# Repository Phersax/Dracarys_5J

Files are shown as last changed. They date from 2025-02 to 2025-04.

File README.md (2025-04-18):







## About the Project
Welcome to the repository dedicated to the development of a 5-degree-of-freedom anthropomorphic robotic arm inspired by the robots Niryo Ned 2 and Kauda! This project aims to create a modular, fully 3D-printable, and open-source manipulator, making it accessible and reproducible for everyone.

The system uses stepper motors to ensure precise movements and features components manufactured through 3D printing. The hardware includes dedicated drivers and a control board to execute smooth trajectories with trapezoidal motion profiles.

In this repository, you’ll find everything you need: 3D models, electronic schematics, control code, and validation tests. Feel free to contribute, improve, and experiment! 

<p align="center">
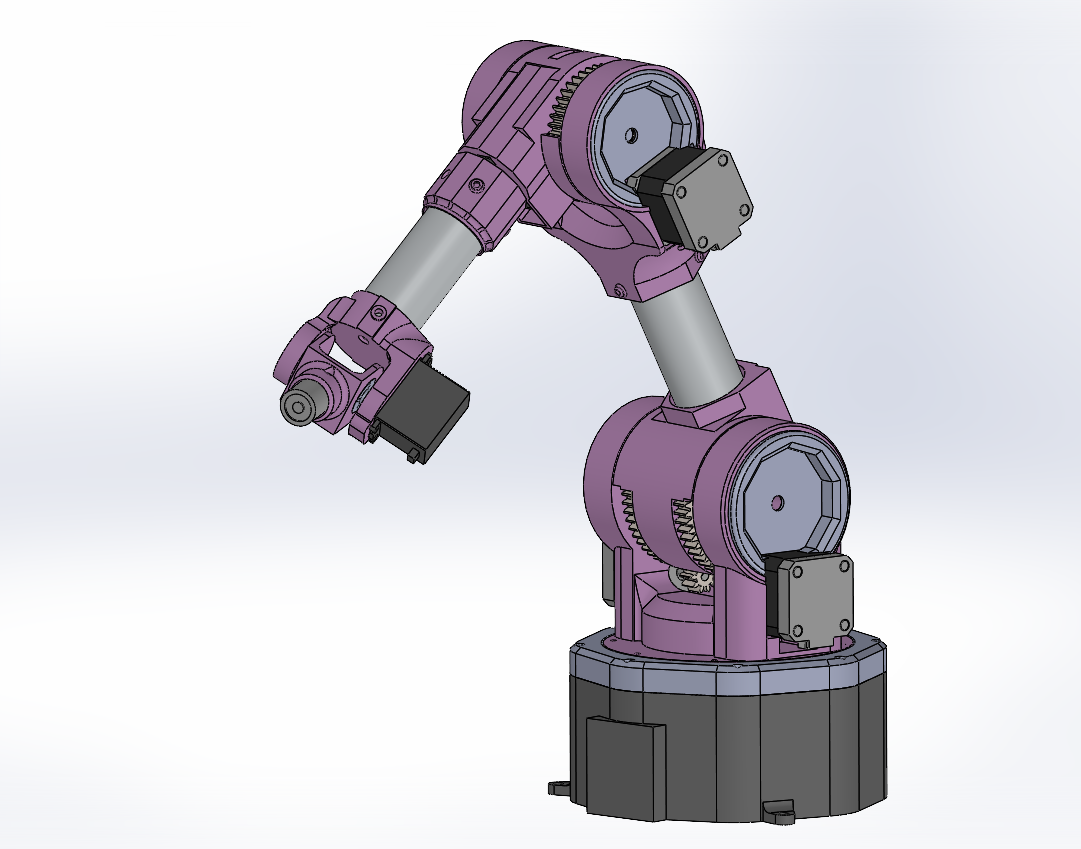
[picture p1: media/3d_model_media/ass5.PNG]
  
</p>

More pictures and videos in the media folder!

## 3D model made with Solidworks
<p align="center">
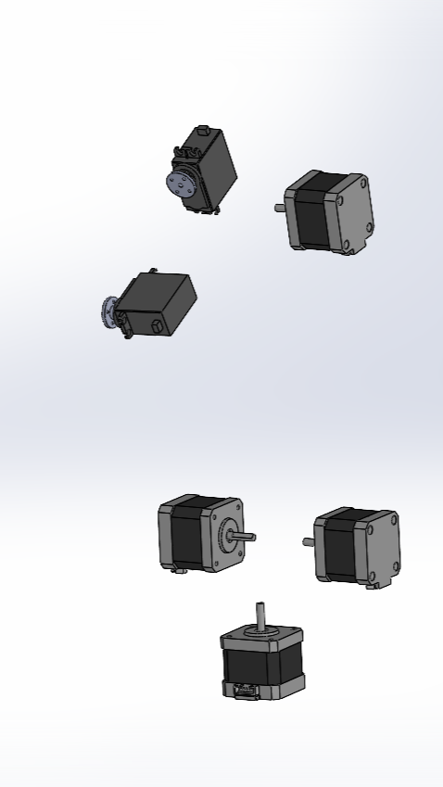
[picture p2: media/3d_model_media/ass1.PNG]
  
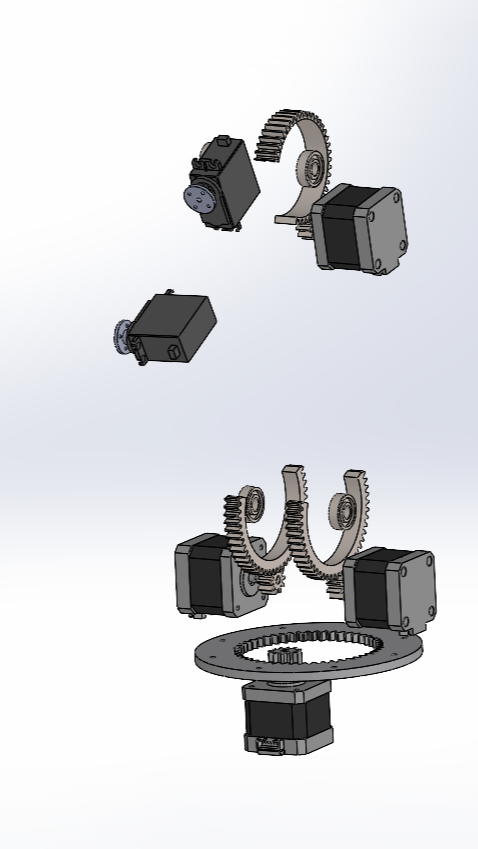
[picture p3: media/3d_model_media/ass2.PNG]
  
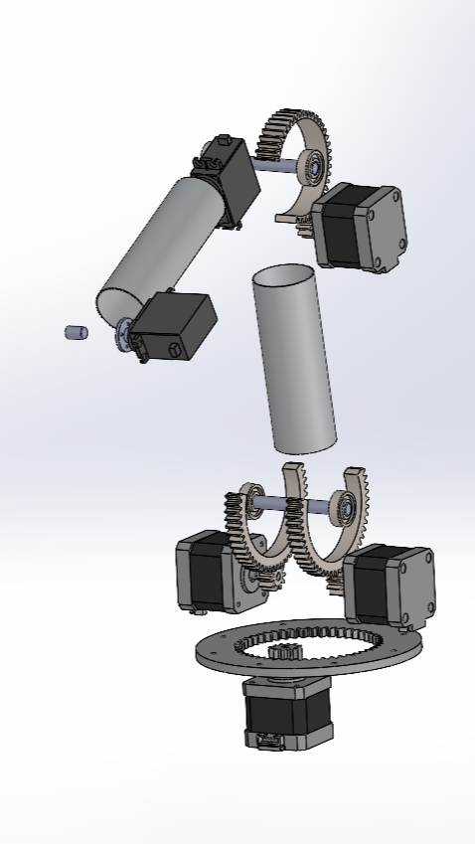
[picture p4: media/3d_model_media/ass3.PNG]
  
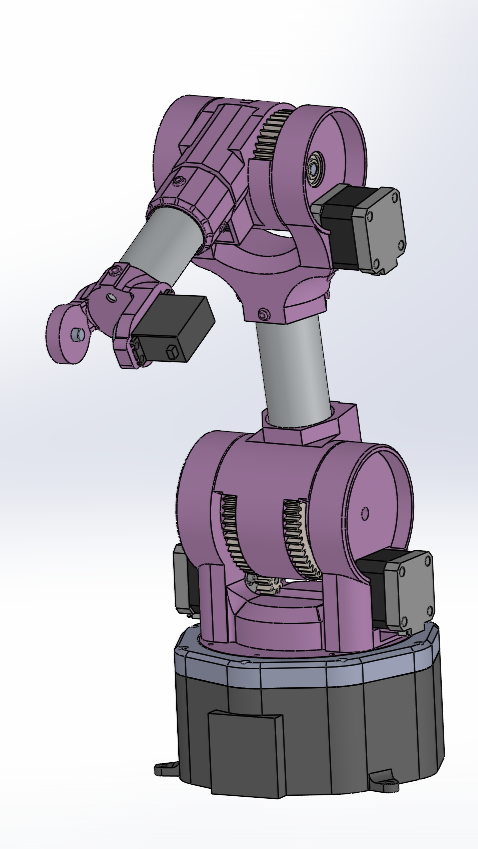
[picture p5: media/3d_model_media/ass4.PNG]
  
</p>

## Schematic
<p align="center">
  
</p>

## Software Notes

All software was developed on the STM32CubeIde and additionally the STM32CubeMx for configuration; for kinematics calculation, on the other hand, MATLAB and the Robotics System Toolbox were used. You may need to download this software in order to load the code properly.

The V1.0_gripper is the main folder of the whole code, anyway you can see for trajectories tested example in the folder v1.0_traj or the 'interrupt_vers' if you're looking for the implementation based on all interrupts. 

If you don't want to use the trapezoidal profile just comment the code as mentioned above, be sure that the timers are set in interrupt mode and check for __HAL_TIM_Base_Start_IT.

For the stepper motor the timers were configured in a chain with master-slave synchronization to count the steps taken according to the rising-edges of the pwm signal and slightly readjusted later to implement the trapezoidal profile. For full configuration details and code insights, links to pdfs are provided in the following section.

The stepper motor control libraries have been implemented to be as general as possible but still refer to the specific manipulator configuration, specifically: 
for joint 1 and joint 3, 1 motor is used; for joint 2, 2 mirrored motors are used, facing each other. Consequently in the stepper library and also partly in the trapezoidal control there are controls for the specific timer of joint 2, which has been treated differently as is the thought configuration. In case one wanted to change software configuration and use for example 1 channel (or 2) for all motors it would be enough to delete (or change) the controls within the libraries and the initial configuration with STM32CubeMx.

## Additional info
Check out the report if you are interested in our work!

[Link to the report](Dr5_report.pdf)

[Link to the pinout and configuration](Dr5_pinout&configuration.pdf)

## License 
Dracarys_5J © 2025 by Francesco Stasi, Davide Tonti is licensed under CC BY-NC-SA 4.0

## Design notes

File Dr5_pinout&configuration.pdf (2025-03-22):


21/03/2025

robotic_arm Project
Configuration Report

## 1. Description

### 1.1. Project

Project Name | robotic_arm
Board Name | NUCLEO-F446RE
Generated with: | STM32CubeMX 6.12.1
Date | 03/21/2025

### 1.2. MCU

MCU Series | STM32F4
MCU Line | STM32F446
MCU name | STM32F446RETx
MCU Package | LQFP64
MCU Pin number | 64

### 1.3. Core(s) information

Core(s) | Arm Cortex-M4

## 2. Pinout Configuration

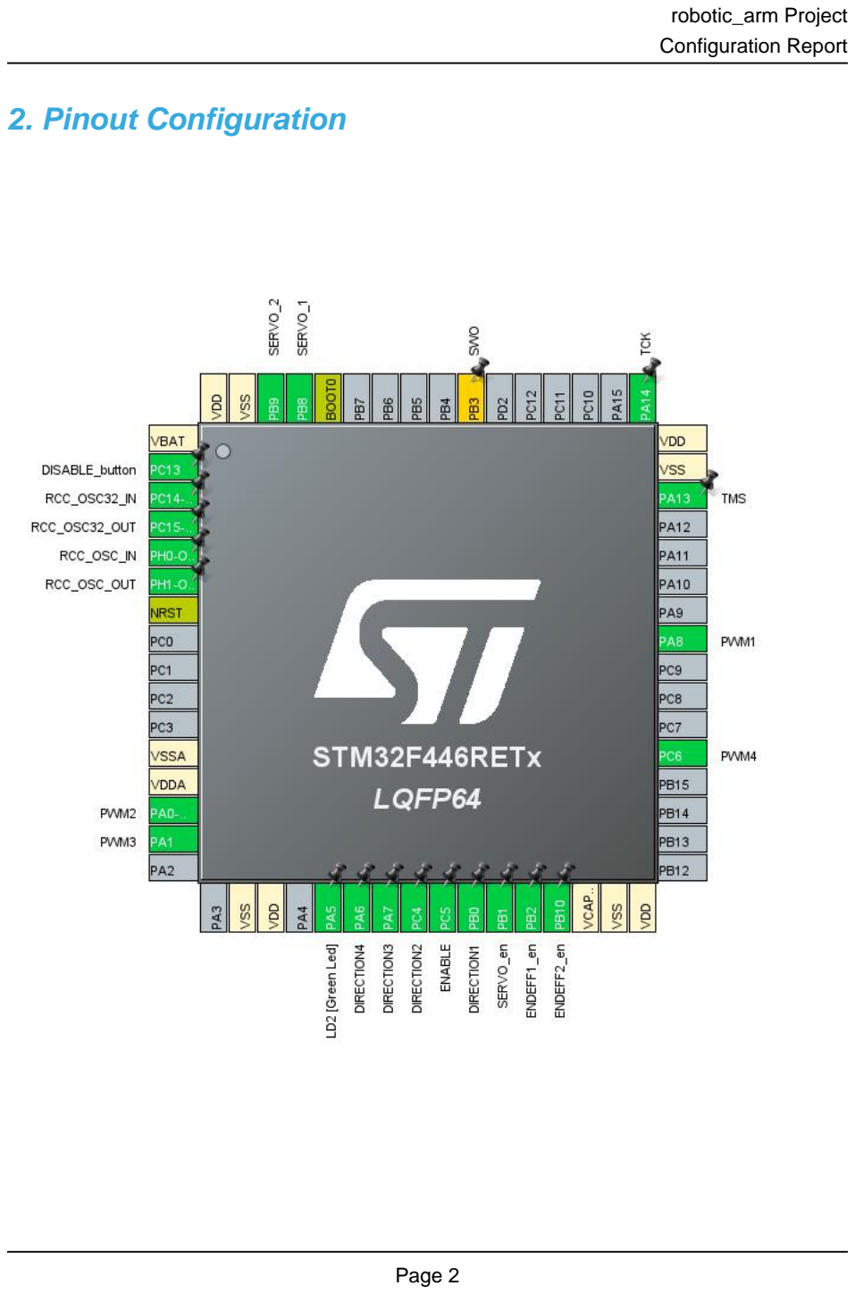
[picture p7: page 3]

## 3. Pins Configuration

Pin Number LQFP64 | Pin Name (function after reset) | Pin Type | Alternate Function(s) | Label
1 | VBAT | Power
2 | PC13 | I/O | GPIO_EXTI13 | DISABLE_button
3 | PC14-OSC32_IN | I/O | RCC_OSC32_IN
4 | PC15-OSC32_OUT | I/O | RCC_OSC32_OUT
5 | PH0-OSC_IN | I/O | RCC_OSC_IN
6 | PH1-OSC_OUT | I/O | RCC_OSC_OUT
7 | NRST | Reset
12 | VSSA | Power
13 | VDDA | Power
14 | PA0-WKUP | I/O | TIM2_CH1 | PWM2
15 | PA1 | I/O | TIM2_CH2 | PWM3
18 | VSS | Power
19 | VDD | Power
21 | PA5 * | I/O | GPIO_Output | LD2 [Green Led]
22 | PA6 * | I/O | GPIO_Output | DIRECTION4
23 | PA7 * | I/O | GPIO_Output | DIRECTION3
24 | PC4 * | I/O | GPIO_Output | DIRECTION2
25 | PC5 * | I/O | GPIO_Output | ENABLE
26 | PB0 * | I/O | GPIO_Output | DIRECTION1
27 | PB1 * | I/O | GPIO_Output | SERVO_en
28 | PB2 * | I/O | GPIO_Output | ENDEFF1_en
29 | PB10 * | I/O | GPIO_Output | ENDEFF2_en
30 | VCAP_1 | Power
31 | VSS | Power
32 | VDD | Power
37 | PC6 | I/O | TIM8_CH1 | PWM4
41 | PA8 | I/O | TIM1_CH1 | PWM1
46 | PA13 | I/O | SYS_JTMS-SWDIO | TMS
47 | VSS | Power
48 | VDD | Power
49 | PA14 | I/O | SYS_JTCK-SWCLK | TCK
55 | PB3 ** | I/O | SYS_JTDO-SWO | SWO
60 | BOOT0 | Boot
61 | PB8 | I/O | TIM10_CH1 | SERVO_1
62 | PB9 | I/O | TIM11_CH1 | SERVO_2
63 | VSS | Power

Pin Number LQFP64 | Pin Name (function after reset) | Pin Type | Alternate Function(s) | Label
64 | VDD | Power

* The pin is affected with an I/O function
** The pin is affected with a peripheral function but no peripheral mode is activated

## 4. Clock Tree Configuration

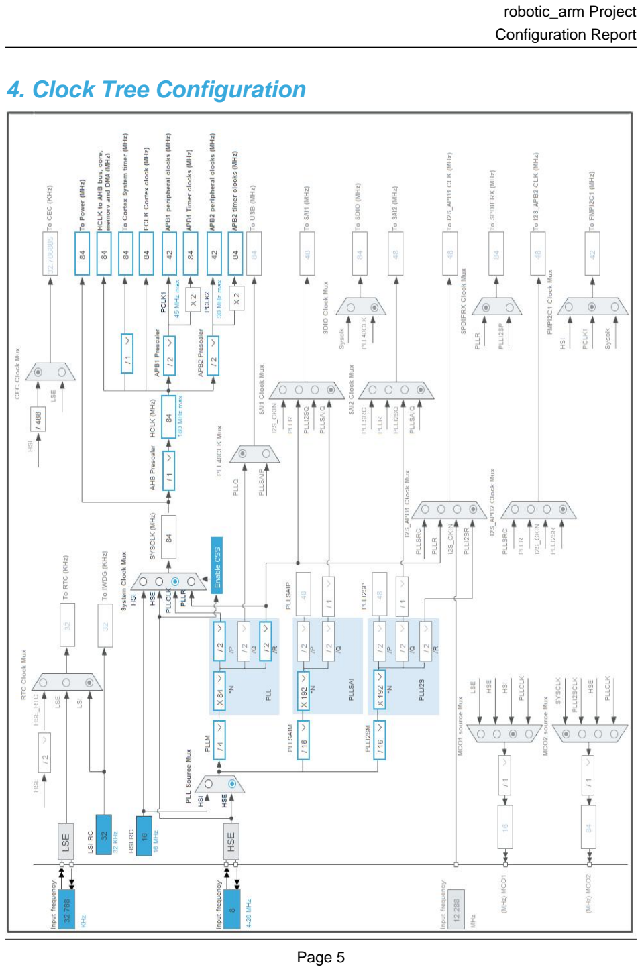
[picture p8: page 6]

## 1. Power Consumption Calculator report

### 1.1. Microcontroller Selection

Series | STM32F4
Line | STM32F446
MCU | STM32F446RETx
Datasheet | DS10693_Rev6

### 1.2. Parameter Selection

Temperature | 25
Vdd | 3.3

### 1.3. Battery Selection

Battery | Li-SOCL2(A3400)
Capacity | 3400.0 mAh
Self Discharge | 0.08 %/month
Nominal Voltage | 3.6 V
Max Cont Current | 100.0 mA
Max Pulse Current | 200.0 mA
Cells in series | 1
Cells in parallel | 1

### 1.4. Sequence

Step | Step1 | Step2
Mode | RUN | STOP_UDM (Under Drive)
Vdd | 3.3 | 3.3
Voltage Source | Battery | Battery
Range | Scale1-High | No Scale
Fetch Type | RAM/FLASH/REGON/ART/P REFETCH | n/a
CPU Frequency | 180 MHz | 0 Hz
Clock Configuration | HSE PLL | Regulator_LP Flash-PwrDwn
Clock Source Frequency | 4 MHz | 0 Hz
Peripherals
Additional Cons. | 0 mA | 0 mA
Average Current | 46 mA | 55 µA
Duration | 0.1 ms | 0.9 ms
DMIPS | 225.0 | 0.0
Ta Max | 98.02 | 104.99
Category | In DS Table | In DS Table

### 1.5. Results

Sequence Time | 1 ms | Average Current | 4.65 mA
Battery Life | 1 month | Average DMIPS | 225.0 DMIPS

### 1.6. Chart

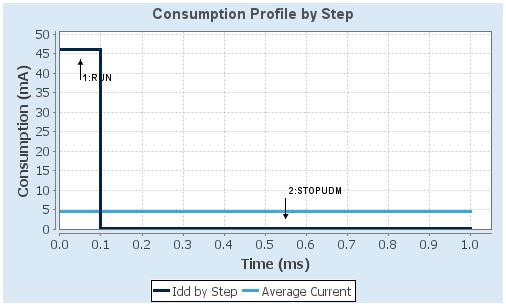
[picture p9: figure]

## 2. Software Project

### 2.1. Project Settings

Name | Value
Project Name | robotic_arm
Project Folder | C:\Users\david\Desktop\v1.0_gripper\Main\robotic_arm
Toolchain / IDE | STM32CubeIDE
Firmware Package Name and Version | STM32Cube FW_F4 V1.28.1
Application Structure | Advanced
Generate Under Root | Yes
Do not generate the main() | No
Minimum Heap Size | 0x200
Minimum Stack Size | 0x400

### 2.2. Code Generation Settings

Name | Value
STM32Cube MCU packages and embedded software | Copy only the necessary library files
Generate peripheral initialization as a pair of '.c/.h' files | Yes
Backup previously generated files when re-generating | No
Keep User Code when re-generating | Yes
Delete previously generated files when not re-generated | Yes
Set all free pins as analog (to optimize the power consumption) | No
Enable Full Assert | No

### 2.3. Advanced Settings - Generated Function Calls

Rank | Function Name | Peripheral Instance Name
1 | SystemClock_Config | RCC
2 | MX_GPIO_Init | GPIO
3 | MX_TIM3_Init | TIM3
4 | MX_TIM5_Init | TIM5
5 | MX_TIM1_Init | TIM1
6 | MX_TIM2_Init | TIM2
7 | MX_TIM4_Init | TIM4
8 | MX_TIM8_Init | TIM8
9 | MX_TIM10_Init | TIM10
10 | MX_TIM11_Init | TIM11
11 | MX_TIM6_Init | TIM6

## 3. Peripherals and Middlewares Configuration

### 3.1. RCC

High Speed Clock (HSE): Crystal/Ceramic Resonator
Low Speed Clock (LSE) : Crystal/Ceramic Resonator
3.1.1. Parameter Settings:

System Parameters:

VDD voltage (V) | 3.3
Instruction Cache | Enabled
Prefetch Buffer | Enabled
Data Cache | Enabled
Flash Latency(WS) | 2 WS (3 CPU cycle)
RCC Parameters:
HSI Calibration Value | 16
TIM Prescaler Selection | Disabled
HSE Startup Timout Value (ms) | 100
LSE Startup Timout Value (ms) | 5000
Power Parameters:
Power Regulator Voltage Scale | Power Regulator Voltage Scale 3
Power Over Drive | Disabled

### 3.2. SYS

Debug: Serial Wire
Timebase Source: SysTick

### 3.3. TIM1

Clock Source : Internal Clock Channel1: PWM Generation CH1
3.3.1. Parameter Settings:

Counter Settings:

Prescaler (PSC - 16 bits value) | 4 *
Counter Mode | Up
Counter Period (AutoReload Register - 16 bits value ) | 65535
Internal Clock Division (CKD) | No Division
Repetition Counter (RCR - 8 bits value) | 0
auto-reload preload | Enable *

Trigger Output (TRGO) Parameters:
Master/Slave Mode (MSM bit) | Enable (Trigger delayed for master/slaves simultaneous start) *
Trigger Event Selection | Update Event *
Break And Dead Time management - BRK Configuration:
BRK State | Disable
BRK Polarity | High
Break And Dead Time management - Output Configuration:
Automatic Output State | Disable
Off State Selection for Run Mode (OSSR) | Disable
Off State Selection for Idle Mode (OSSI) | Disable
Lock Configuration | Off
PWM Generation Channel 1:
Mode | PWM mode 1
Pulse (16 bits value) | 32768 *
Output compare preload | Enable
Fast Mode | Enable *
CH Polarity | High
CH Idle State | Reset

### 3.4. TIM2

Clock Source : Internal Clock Channel1: PWM Generation CH1 Channel2: PWM Generation CH2
3.4.1. Parameter Settings:

Counter Settings:

Prescaler (PSC - 16 bits value) | 4 *
Counter Mode | Up
Counter Period (AutoReload Register - 32 bits value ) | 65535 *
Internal Clock Division (CKD) | No Division
auto-reload preload | Enable *
Trigger Output (TRGO) Parameters:
Master/Slave Mode (MSM bit) | Enable (Trigger delayed for master/slaves simultaneous start) *
Trigger Event Selection | Update Event *
PWM Generation Channel 1:

Mode | PWM mode 1
Pulse (32 bits value) | 32768 *
Output compare preload | Enable
Fast Mode | Enable *
CH Polarity | High
PWM Generation Channel 2:
Mode | PWM mode 1
Pulse (32 bits value) | 32768 *
Output compare preload | Enable
Fast Mode | Enable *
CH Polarity | High

### 3.5. TIM3

Slave Mode: Trigger Mode
Trigger Source: ITR1
Clock Source : Internal Clock
3.5.1. Parameter Settings:

Counter Settings:

Prescaler (PSC - 16 bits value) | 65535 *
Counter Mode | Up
Counter Period (AutoReload Register - 16 bits value ) | 199 *
Internal Clock Division (CKD) | No Division
auto-reload preload | Enable *
Slave Mode Controller | Trigger Mode
Trigger Output (TRGO) Parameters:
Master/Slave Mode (MSM bit) | Disable (Trigger input effect not delayed)
Trigger Event Selection | Reset (UG bit from TIMx_EGR)

### 3.6. TIM4

Slave Mode: Trigger Mode
Trigger Source: ITR0
mode: Clock Source
3.6.1. Parameter Settings:

Counter Settings:

Prescaler (PSC - 16 bits value) | 65535 *
Counter Mode | Up
Counter Period (AutoReload Register - 16 bits value ) | 199 *
Internal Clock Division (CKD) | No Division
auto-reload preload | Enable *
Slave Mode Controller | Trigger Mode
Trigger Output (TRGO) Parameters:
Master/Slave Mode (MSM bit) | Disable (Trigger input effect not delayed)
Trigger Event Selection | Reset (UG bit from TIMx_EGR)

### 3.7. TIM5

Slave Mode: Trigger Mode
Trigger Source: ITR3
mode: Clock Source
3.7.1. Parameter Settings:

Counter Settings:

Prescaler (PSC - 16 bits value) | 65535 *
Counter Mode | Up
Counter Period (AutoReload Register - 32 bits value ) | 199 *
Internal Clock Division (CKD) | No Division
auto-reload preload | Disable
Slave Mode Controller | Trigger Mode
Trigger Output (TRGO) Parameters:
Master/Slave Mode (MSM bit) | Disable (Trigger input effect not delayed)
Trigger Event Selection | Reset (UG bit from TIMx_EGR)

### 3.8. TIM6

mode: Activated
3.8.1. Parameter Settings:

Counter Settings:

Prescaler (PSC - 16 bits value) | 27 *
Counter Mode | Up
Counter Period (AutoReload Register - 16 bits value ) | 1400 *
auto-reload preload | Disable

Trigger Output (TRGO) Parameters:

Trigger Event Selection | Reset (UG bit from TIMx_EGR)

### 3.9. TIM8

Clock Source : Internal Clock
Channel1: PWM Generation CH1
3.9.1. Parameter Settings:

Counter Settings:

Prescaler (PSC - 16 bits value) | 4 *
Counter Mode | Up
Counter Period (AutoReload Register - 16 bits value ) | 65535
Internal Clock Division (CKD) | No Division
Repetition Counter (RCR - 8 bits value) | 0
auto-reload preload | Enable *
Trigger Output (TRGO) Parameters:
Master/Slave Mode (MSM bit) | Enable (Trigger delayed for master/slaves simultaneous start) *
Trigger Event Selection | Update Event *
Break And Dead Time management - BRK Configuration:
BRK State | Disable
BRK Polarity | High
Break And Dead Time management - Output Configuration:
Automatic Output State | Disable
Off State Selection for Run Mode (OSSR) | Disable
Off State Selection for Idle Mode (OSSI) | Disable
Lock Configuration | Off
PWM Generation Channel 1:
Mode | PWM mode 1
Pulse (16 bits value) | 32768 *
Output compare preload | Enable
Fast Mode | Enable *
CH Polarity | High
CH Idle State | Reset

### 3.10. TIM10

mode: Activated
Channel1: PWM Generation CH1
3.10.1. Parameter Settings:

Counter Settings:

Prescaler (PSC - 16 bits value) | 0
Counter Mode | Up
Counter Period (AutoReload Register - 16 bits value ) | 65535
Internal Clock Division (CKD) | No Division
auto-reload preload | Enable *
PWM Generation Channel 1:
Mode | PWM mode 1
Pulse (16 bits value) | 1 *
Output compare preload | Enable
Fast Mode | Enable *
CH Polarity | High

### 3.11. TIM11

mode: Activated
Channel1: PWM Generation CH1
3.11.1. Parameter Settings:

Counter Settings:

Prescaler (PSC - 16 bits value) | 0
Counter Mode | Up
Counter Period (AutoReload Register - 16 bits value ) | 65535
Internal Clock Division (CKD) | No Division
auto-reload preload | Enable *
PWM Generation Channel 1:
Mode | PWM mode 1
Pulse (16 bits value) | 1 *
Output compare preload | Enable
Fast Mode | Enable *
CH Polarity | High

* User modified value

## 4. System Configuration

### 4.1. GPIO configuration

IP | Pin | Signal | GPIO mode | GPIO pull/up pull down | Max Speed | User Label
RCC | PC14-OSC32_IN | RCC_OSC32_IN | n/a | n/a | n/a
| PC15-OSC32_OU T | RCC_OSC32_O UT | n/a | n/a | n/a
| PH0-OSC_IN | RCC_OSC_IN | n/a | n/a | n/a
| PH1-OSC_OUT | RCC_OSC_OUT | n/a | n/a | n/a
SYS | PA13 | SYS_JTMS-SWDIO | n/a | n/a | n/a | TMS
| PA14 | SYS_JTCK-SWCLK | n/a | n/a | n/a | TCK
TIM1 | PA8 | TIM1_CH1 | Alternate Function Push Pull | No pull-up and no pull-down | Low | PWM1
TIM2 | PA0-WKUP | TIM2_CH1 | Alternate Function Push Pull | No pull-up and no pull-down | Low | PWM2
| PA1 | TIM2_CH2 | Alternate Function Push Pull | No pull-up and no pull-down | Low | PWM3
TIM8 | PC6 | TIM8_CH1 | Alternate Function Push Pull | No pull-up and no pull-down | Low | PWM4
TIM10 | PB8 | TIM10_CH1 | Alternate Function Push Pull | No pull-up and no pull-down | Low | SERVO_1
TIM11 | PB9 | TIM11_CH1 | Alternate Function Push Pull | No pull-up and no pull-down | Low | SERVO_2
Single Mapped Signals | PB3 | SYS_JTDO-SWO | n/a | n/a | n/a | SWO
GPIO | PC13 | GPIO_EXTI13 | External Interrupt Mode with Rising edge trigger detection | No pull-up and no pull-down | n/a | DISABLE_button
| PA5 | GPIO_Output | Output Push Pull | No pull-up and no pull-down | Low | LD2 [Green Led]
| PA6 | GPIO_Output | Output Push Pull | Pull-down * | Low | DIRECTION4
| PA7 | GPIO_Output | Output Push Pull | Pull-down * | Low | DIRECTION3
| PC4 | GPIO_Output | Output Push Pull | Pull-down * | Low | DIRECTION2
| PC5 | GPIO_Output | Output Push Pull | Pull-up * | High * | ENABLE
| PB0 | GPIO_Output | Output Push Pull | Pull-down * | Low | DIRECTION1
| PB1 | GPIO_Output | Output Push Pull | Pull-down * | Low | SERVO_en
| PB2 | GPIO_Output | Output Push Pull | Pull-up * | Low | ENDEFF1_en
| PB10 | GPIO_Output | Output Push Pull | Pull-up * | Low | ENDEFF2_en

### 4.2. DMA configuration

nothing configured in DMA service

### 4.3. NVIC configuration

4.3.1. NVIC
Interrupt Table | Enable | Preenmption Priority | SubPriority
Non maskable interrupt | true | 0 | 0
Hard fault interrupt | true | 0 | 0
Memory management fault | true | 0 | 0
Pre-fetch fault, memory access fault | true | 0 | 0
Undefined instruction or illegal state | true | 0 | 0
System service call via SWI instruction | true | 0 | 0
Debug monitor | true | 0 | 0
Pendable request for system service | true | 0 | 0
System tick timer | true | 0 | 0
TIM1 capture compare interrupt | true | 1 | 0
TIM2 global interrupt | true | 1 | 0
EXTI line[15:10] interrupts | true | 0 | 0
TIM8 break interrupt and TIM12 global interrupt | true | 1 | 0
TIM8 update interrupt and TIM13 global interrupt | true | 1 | 0
TIM8 trigger and commutation interrupts and TIM14 global interrupt | true | 1 | 0
TIM8 capture compare interrupt | true | 1 | 0
TIM6 global interrupt and DAC1, DAC2 underrun error interrupts | true | 0 | 0
PVD interrupt through EXTI line 16 | | unused
Flash global interrupt | | unused
RCC global interrupt | | unused
TIM1 break interrupt and TIM9 global interrupt | | unused
TIM1 update interrupt and TIM10 global interrupt | | unused
TIM1 trigger and commutation interrupts and TIM11 global interrupt | | unused
TIM3 global interrupt | | unused
TIM4 global interrupt | | unused
TIM5 global interrupt | | unused
FPU global interrupt | | unused
4.3.2. NVIC Code generation

Enabled interrupt Table Select for init
sequence ordering
| | Generate IRQ
| | handler | Call HAL handler
Non maskable interrupt | false | true | false
Hard fault interrupt | false | true | false

Enabled interrupt Table | Select for init sequence ordering | Generate IRQ handler | Call HAL handler
Memory management fault | false | true | false
Pre-fetch fault, memory access fault | false | true | false
Undefined instruction or illegal state | false | true | false
System service call via SWI instruction | false | true | false
Debug monitor | false | true | false
Pendable request for system service | false | true | false
System tick timer | false | true | true
TIM1 capture compare interrupt | false | true | true
TIM2 global interrupt | false | true | true
EXTI line[15:10] interrupts | false | true | true
TIM8 break interrupt and TIM12 global interrupt | false | true | true
TIM8 update interrupt and TIM13 global interrupt | false | true | true
TIM8 trigger and commutation interrupts and TIM14 global interrupt | false | true | true
TIM8 capture compare interrupt | false | true | true
TIM6 global interrupt and DAC1, DAC2 underrun error interrupts | false | true | true

* User modified value

## 5. System Views

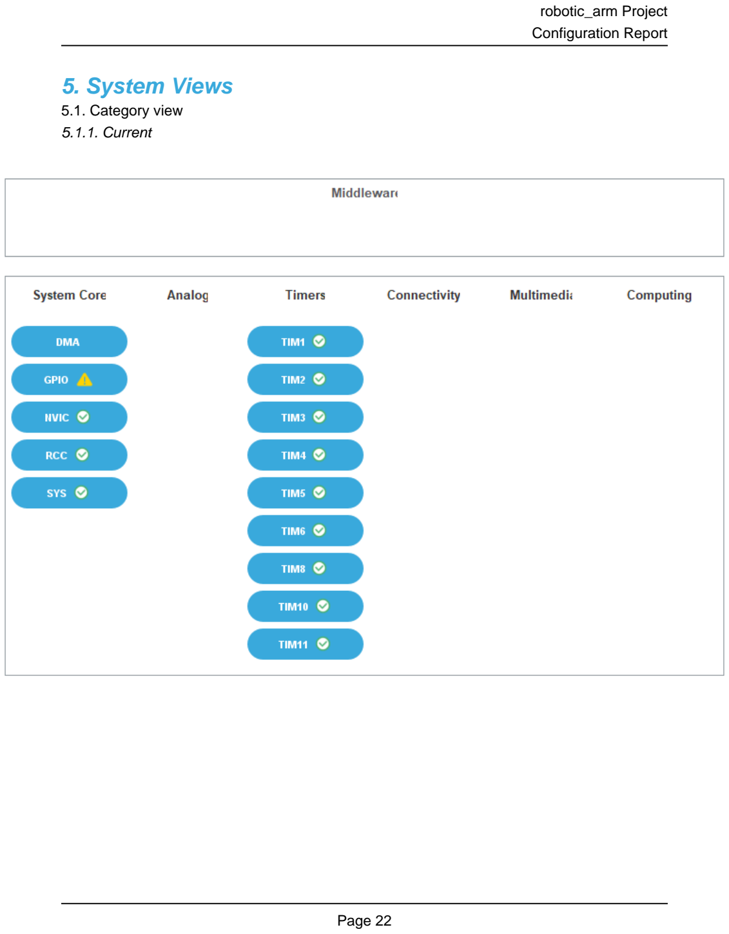
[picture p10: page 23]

5.1. Category view
5.1.1. Current

## 6. Docs & Resources

Type | Link
BSDL files | https://www.st.com/resource/en/bsdl_model/stm32f446_bsdl.zip
IBIS models | https://www.st.com/resource/en/ibis_model/stm32f446_ibis.zip
System View Description | https://www.st.com/resource/en/svd/stm32f4-svd.zip
Presentations | https://www.st.com/resource/en/product_presentation/stm32-stm8_embedded_software_solutions.pdf
Presentations | https://www.st.com/resource/en/product_presentation/stm32_eval-tools_portfolio.pdf
Presentations | https://www.st.com/resource/en/product_presentation/stm32_stm8_functi onal-safety-packages.pdf
Presentations | https://www.st.com/resource/en/product_presentation/stm32-stm8_software_development_tools.pdf
Presentations | https://www.st.com/resource/en/product_presentation/microcontrollers-stm32-family-overview.pdf
Brochures | https://www.st.com/resource/en/brochure/products-and-solutions-for-plcs-and-smart-i-os.pdf
Flyers | https://www.st.com/resource/en/flyer/flstm32nucleo.pdf
Flyers | https://www.st.com/resource/en/flyer/flstm32trust.pdf
Product Certifications | https://www.st.com/resource/en/certification_document/stm32_authentication_can.pdf
Application Notes | https://www.st.com/resource/en/application_note/an1709-emc-design-guide-for-stm8-stm32-and-legacy-mcus-stmicroelectronics.pdf
Application Notes | https://www.st.com/resource/en/application_note/an2606-stm32-microcontroller-system-memory-boot-mode-stmicroelectronics.pdf
Application Notes | https://www.st.com/resource/en/application_note/an2945-stm8s-and-stm32-mcus-a-consistent-832bit-product-line-for-painless-migration-stmicroelectronics.pdf
Application Notes | https://www.st.com/resource/en/application_note/an3070-managing-the- driver-enable-signal-for-rs485-and-iolink-communications-with-the-

| stm32s-usart-stmicroelectronics.pdf
Application Notes | https://www.st.com/resource/en/application_note/an3126-audio-and-waveform-generation-using-the-dac-in-stm32-products-stmicroelectronics.pdf
Application Notes | https://www.st.com/resource/en/application_note/an3154-can-protocol-used-in-the-stm32-bootloader-stmicroelectronics.pdf
Application Notes | https://www.st.com/resource/en/application_note/an3155-usart-protocol-used-in-the-stm32-bootloader-stmicroelectronics.pdf
Application Notes | https://www.st.com/resource/en/application_note/an3156-usb-dfu-protocol-used-in-the-stm32-bootloader-stmicroelectronics.pdf
Application Notes | https://www.st.com/resource/en/application_note/an3364-migration-and-compatibility-guidelines-for-stm32-microcontroller-applications-stmicroelectronics.pdf
Application Notes | https://www.st.com/resource/en/application_note/an3997-audio-playback-and-recording-using-the-stm32f4discovery-stmicroelectronics.pdf
Application Notes | https://www.st.com/resource/en/application_note/an3998-pdm-audio-software-decoding-on-stm32-microcontrollers-stmicroelectronics.pdf
Application Notes | https://www.st.com/resource/en/application_note/an4031-using-the-stm32f2-stm32f4-and-stm32f7-series-dma-controller-stmicroelectronics.pdf
Application Notes | https://www.st.com/resource/en/application_note/an4221-i2c-protocol-used-in-the-stm32-bootloader-stmicroelectronics.pdf
Application Notes | https://www.st.com/resource/en/application_note/an4286-spi-protocol-used-in-the-stm32-bootloader-stmicroelectronics.pdf
Application Notes | https://www.st.com/resource/en/application_note/an4488-getting-started-with-stm32f4xxxx-mcu-hardware-development-stmicroelectronics.pdf
Application Notes | https://www.st.com/resource/en/application_note/an4566-extending-the-dac-performance-of-stm32-microcontrollers-stmicroelectronics.pdf
Application Notes | https://www.st.com/resource/en/application_note/an4640-peripherals-interconnections-on-stm32f4057xx-stm32f4157xx-stm32f42xxx-stm32f43xxx-stm32f446xx-and-stm32f469479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
Application Notes | https://www.st.com/resource/en/application_note/an4655-virtually- increasing-the-number-of-serial-communication-peripherals-in-stm32-

| applications-stmicroelectronics.pdf
Application Notes | https://www.st.com/resource/en/application_note/an4658-migration-of-applications-from-stm32f429439-lines-to-stm32f446-line-stmicroelectronics.pdf
Application Notes | https://www.st.com/resource/en/application_note/an4739-stm32cube-firmware-examples-for-stm32f4-series-stmicroelectronics.pdf
Application Notes | https://www.st.com/resource/en/application_note/an4750-handling-of-soft-errors-in-stm32-applications-stmicroelectronics.pdf
Application Notes | https://www.st.com/resource/en/application_note/an4776-generalpurpose-timer-cookbook-for-stm32-microcontrollers-stmicroelectronics.pdf
Application Notes | https://www.st.com/resource/en/application_note/an4803-highspeed-si-simulations-using-ibis-and-boardlevel-simulations-using-hyperlynx-si-on-stm32-mcus-and-mpus-stmic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
Application Notes | https://www.st.com/resource/en/application_note/an4850-stm32-mcus-spreadspectrum-clock-generation-principles-properties-and-implementation-stmicroelectronics.pdf
Application Notes | https://www.st.com/resource/en/application_note/an4989-stm32-microcontroller-debug-toolbox-stmicroelectronics.pdf
Application Notes | https://www.st.com/resource/en/application_note/an4995-using-an-electromyogram-technique-to-detect-muscle-activity-stmicroelectronics.pdf
Application Notes | https://www.st.com/resource/en/application_note/an5027-interfacing-pdm-digital-microphones-using-stm32-mcus-and-mpus-stmicroelectronics.pdf
Application Notes | https://www.st.com/resource/en/application_note/an5073-receiving-spdif-audio-stream-with-the-stm32f4f7h7-series-stmicroelectronics.pdf
Application Notes | https://www.st.com/resource/en/application_note/an4760-quadspi-interface-on-stm32-microcontrollers-and-microprocessors--stmicroelectronics.pdf
Application Notes | https://www.st.com/resource/en/application_note/an4899-stm32-microcontroller-gpio-hardware-settings-and-lowpower-consumption-stmicroelectronics.pdf
Application Notes | https://www.st.com/resource/en/application_note/an5612-esd-protection-of-stm32-mcus-and-mpus-stmicroelectronics.pdf

Application Notes | https://www.st.com/resource/en/application_note/an4838-introduction-to-memory-protection-unit-management-on-stm32-mcus-stmicroelectronics.pdf
Application Notes | https://www.st.com/resource/en/application_note/an4879-introduction-to-usb-hardware-and-pcb-guidelines-using-stm32-mcus-stmicroelectronics.pdf
Application Notes | https://www.st.com/resource/en/application_note/an5225-introduction-to-usb-typec-power-delivery-for-stm32-mcus-and-mpus-stmicroelectronics.pdf
Application Notes | https://www.st.com/resource/en/application_note/an5537-how-to-use-adc-oversampling-techniques-to-improve-signaltonoise-ratio-on-stm32-mcus-stmicroelectronics.pdf
Application Notes | https://www.st.com/resource/en/application_note/an5036-guidelines-for-thermal-management-on-stm32-applications-stmicroelectronics.pdf
Application Notes | https://www.st.com/resource/en/application_note/an4230-introduction-to-random-number-generation-validation-using-the-nist-statistical-test-suite-for-stm32-mcus-and-m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
Application Notes | https://www.st.com/resource/en/application_note/an2867-guidelines-for-oscillator-design-on-stm8afals-and-stm32-mcusmpus-stmicroelectronics.pdf
Application Notes | https://www.st.com/resource/en/application_note/an4013-introduction-to-timers-for-stm32-mcus-stmicroelectronics.pdf
Application Notes | https://www.st.com/resource/en/application_note/an4277-how-to-use-pwm-shutdown-for-motor-control-and-digital-power-conversion-on-stm32-mcus-stmicroelectronics.pdf
Application Notes | https://www.st.com/resource/en/application_note/an4759-introduction-to-using-the-hardware-realtime-clock-rtc-and-the-tamper-management-unit-tamp-with-stm32-mcus-stmi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
Application Notes | https://www.st.com/resource/en/application_note/an4908-getting-started-with-usart-automatic-baud-rater-detection-for-stm32-mcus-stmicroelectronics.pdf
Application Notes | https://www.st.com/resource/en/application_note/an5156-introduction-to-security-for-stm32-mcus-stmicroelectronics.pdf
Application Notes | https://www.st.com/resource/en/application_note/an5543-guidelines-for-

| enhanced-spi-communication-on-stm32-mcus-and-mpus-stmicroelectronics.pdf
Application Notes | https://www.st.com/resource/en/application_note/an5992-migrating-from-stm32f446-to-stm32h523533-mcus-stmicroelectronics.pdf
Application Notes | https://www.st.com/resource/en/application_note/cd00211314-how-to-optimize-the-adc-accuracy-in-the-stm32-mcus-stmicroelectronics.pdf
Application Notes | https://www.st.com/resource/en/application_note/an2639-soldering-recommendations-and-package-information-for-leadfree-ecopack2-mcus-and-mpus-stmicroelectronics.pdf
Application Notes | https://www.st.com/resource/en/application_note/an5020-introduction-to-digital-camera-interface-dcmi-for-stm32-mcus-stmicroelectronics.pdf
Application Notes for related Tools & Software | https://www.st.com/resource/en/application_note/an2656-stm32f10xxx-lcd-glass-driver-firmware-stmicroelectronics.pdf
Application Notes for related Tools & Software | https://www.st.com/resource/en/application_note/an2790-tft-lcd-interfacing-with-the-highdensity-stm32f10xxx-fsmc-stmicroelectronics.pdf
Application Notes for related Tools & Software | https://www.st.com/resource/en/application_note/an3078-stm32-inapplication-programming-over-the-ic-bus-stmicroelectronics.pdf
Application Notes for related Tools & Software | https://www.st.com/resource/en/application_note/an3116-stm32s-adc-modes-and-their-applications-stmicroelectronics.pdf
Application Notes for related Tools & Software | https://www.st.com/resource/en/application_note/an3174-implementing-receivers-for-infrared-remote-control-protocols-using-stm32f10xxx-microcontrollers-stmicroelectro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
Application Notes for related Tools & Software | https://www.st.com/resource/en/application_note/an3241-qvga-tftlcd-direct-drive-using-the-stm32f10xx-fsmc-peripheral-stmicroelectronics.pdf
Application Notes for related Tools & Software | https://www.st.com/resource/en/application_note/an3307-guidelines-for-obtaining-iec-60335-class-b-certification-for-any-stm32-application-stmicroelectronics.pdf

Application Notes
for related Tools

https://www.st.com/resource/en/application_note/an3965-stm32f40xstm32f41x-inapplication-programming-using-the-usart-

& Software | stmicroelectronics.pdf
Application Notes for related Tools & Software | https://www.st.com/resource/en/application_note/an3969-eeprom-emulation-in-stm32f40xstm32f41x-microcontrollers-stmicroelectronics.pdf
Application Notes for related Tools & Software | https://www.st.com/resource/en/application_note/an4044-floating-point-unit-demonstration-on-stm32-microcontrollers-stmicroelectronics.pdf
Application Notes for related Tools & Software | https://www.st.com/resource/en/application_note/an4323-getting-started-with-stemwin-library-stmicroelectronics.pdf
Application Notes for related Tools & Software | https://www.st.com/resource/en/application_note/an4365-using-stm32f4-mcu-power-modes-with-best-dynamic-efficiency-stmicroelectronics.pdf
Application Notes for related Tools & Software | https://www.st.com/resource/en/application_note/an4435-guidelines-for-obtaining-ulcsaiec-607301603351-class-b-certification-in-any-stm32-application-stmicroelectroni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
Application Notes for related Tools & Software | https://www.st.com/resource/en/application_note/an4457-implementing-an-emulated-uart-on-stm32f4-microcontrollers-stmicroelectronics.pdf
Application Notes for related Tools & Software | https://www.st.com/resource/en/application_note/an4499-stm32--nrf51822-bluetooth-low-energy-system-solution-stmicroelectronics.pdf
Application Notes for related Tools & Software | https://www.st.com/resource/en/application_note/an4657-stm32-inapplication-programming-iap-using-the-usart-stmicroelectronics.pdf
Application Notes for related Tools & Software | https://www.st.com/resource/en/application_note/an4666-parallel-synchronous-transmission-using-gpio-and-dma-stmicroelectronics.pdf
Application Notes for related Tools & Software | https://www.st.com/resource/en/application_note/an4678-full-duplex-spi-emulation-for-stm32f4-microcontrollers-stmicroelectronics.pdf
Application Notes for related Tools & Software | https://www.st.com/resource/en/application_note/an4701-proprietary-code-readout-protection-on-microcontrollers-of-the-stm32f4-series-stmicroelectronics.pdf

Application Notes for related Tools & Software | https://www.st.com/resource/en/application_note/an4739-stm32cube-firmware-examples-for-stm32f4-series-stmicroelectronics.pdf
Application Notes for related Tools & Software | https://www.st.com/resource/en/application_note/an4758-proprietary-code-readout-protection-on-stm32l4-stm32l4-stm32g4-and-stm32wb-series-mcus-stmicroelectronics.pdf
Application Notes for related Tools & Software | https://www.st.com/resource/en/application_note/an4841-digital-signal-processing-for-stm32-microcontrollers-using-cmsis-stmicroelectronics.pdf
Application Notes for related Tools & Software | https://www.st.com/resource/en/application_note/an4852-programming-an-external-flash-memory-using-the-uart-bootloader-builtin-stm32-microcontrollers-stmicroelectroni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
Application Notes for related Tools & Software | https://www.st.com/resource/en/application_note/an4968-proprietary-code-read-out-protection-pcrop-on-stm32f72xxx-and-stm32f73xxx-microcontrollers-stmicroelectronics.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
Application Notes for related Tools & Software | https://www.st.com/resource/en/application_note/an5056-integration-guide-for-the-xcubesbsfu-stm32cube-expansion-package-stmicroelectronics.pdf
Application Notes for related Tools & Software | https://www.st.com/resource/en/application_note/an5360-getting-started-with-projects-based-on-the-stm32mp1-series-in-stm32cubeide-stmicroelectronics.pdf
Application Notes for related Tools & Software | https://www.st.com/resource/en/application_note/an5361-getting-started-with-projects-based-on-dualcore-stm32h7-microcontrollers-in-stm32cubeide-stmicroelectronics.pd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
Application Notes for related Tools & Software | https://www.st.com/resource/en/application_note/an5394-getting-started-with-projects-based-on-the-stm32l5-series-in-stm32cubeide-stmicroelectronics.pdf
Application Notes for related Tools & Software | https://www.st.com/resource/en/application_note/an5418-how-to-build-a-simple-usbpd-sink-application-with-stm32cubemx-stmicroelectronics.pdf
Application Notes for related Tools & Software | https://www.st.com/resource/en/application_note/an5426-migrating-graphics-middleware-projects-from-stm32cubemx-540-to-stm32cubemx-550-stmicroelectronics.pdf
Application Notes | https://www.st.com/resource/en/application_note/an5464-position-control-

for related Tools & Software | of-a-threephase-permanent-magnet-motor-using-xcubemcsdk-or-xcubemcsdkful-stmicroelectronics.pdf
Application Notes for related Tools & Software | https://www.st.com/resource/en/application_note/an5564-getting-started-with-projects-based-on-dualcore-stm32wl-microcontrollers-in-stm32cubeide-stmicroelectronics.pd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
Application Notes for related Tools & Software | https://www.st.com/resource/en/application_note/an5698-adapting-the-xcubestl-functional-safety-package-for-stm32-iec-61508-compliant-to-other-safety-standards-stmicr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
Application Notes for related Tools & Software | https://www.st.com/resource/en/application_note/an5731-stm32cubemx-and-stm32cubeide-threadsafe-solution-stmicroelectronics.pdf
Application Notes for related Tools & Software | https://www.st.com/resource/en/application_note/an4502-stm32-smbuspmbus-expansion-package-for-stm32cube-stmicroelectronics.pdf
Application Notes for related Tools & Software | https://www.st.com/resource/en/application_note/an5952-how-to-use-cmake-in-stm32cubeide-stmicroelectronics.pdf
Application Notes for related Tools & Software | https://www.st.com/resource/en/application_note/an5054-how-to-perform-secure-programming-using-stm32cubeprogrammer-stmicroelectronics.pdf
Application Notes for related Tools & Software | https://www.st.com/resource/en/application_note/an6179-how-to-integrate-the-stl-firmware-into-a-time-critical-user-application-stmicroelectronics.pdf
Errata Sheets | https://www.st.com/resource/en/errata_sheet/es0298-stm32f446xcxe-device-errata-stmicroelectronics.pdf
Datasheet | https://www.st.com/resource/en/datasheet/dm00141306.pdf
Programming Manuals | https://www.st.com/resource/en/programming_manual/pm0214-stm32-cortexm4-mcus-and-mpus-programming-manual-stmicroelectronics.pdf
Reference Manuals | https://www.st.com/resource/en/reference_manual/rm0390-stm32f446xx-advanced-armbased-32bit-mcus-stmicroelectronics.pdf
Technical Notes & Articles | https://www.st.com/resource/en/technical_note/tn0516-overview-of-the-stm32f0xf100xxf103xx-and-stm32f2xxf30xf4xx-mcus-pmsm-singledual-foc-sdk-v40-stmicroelectronics.p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

Technical Notes & Articles | https://www.st.com/resource/en/technical_note/tn1163-description-of-wlcsp-for-microcontrollers-and-recommendations-for-its-use-stmicroelectronics.pdf
Technical Notes & Articles | https://www.st.com/resource/en/technical_note/tn1204-tape-and-reel-shipping-media-for-stm32-microcontrollers-in-bga-packages-stmicroelectronics.pdf
Technical Notes & Articles | https://www.st.com/resource/en/technical_note/tn1205-tape-and-reel-shipping-media-for-stm8-and-stm32-microcontrollers-in-fpn-packages-stmicroelectronics.pdf
Technical Notes & Articles | https://www.st.com/resource/en/technical_note/tn1206-tape-and-reel-shipping-media-for-stm8-and-stm32-microcontrollers-in-qfp-packages-stmicroelectronics.pdf
Technical Notes & Articles | https://www.st.com/resource/en/technical_note/tn1207-tape-and-reel-shipping-media-for-stm8-and-stm32-microcontrollers-in-so-packages-stmicroelectronics.pdf
Technical Notes & Articles | https://www.st.com/resource/en/technical_note/tn1208-tape-and-reel-shipping-media-for-stm8-and-stm32-microcontrollers-in-tssop-and-ssop-packages-stmicroelectronics.p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
Technical Notes & Articles | https://www.st.com/resource/en/technical_note/tn1433-reference-device-marking-schematics-for-stm32-microcontrollers-and-microprocessors-stmicroelectronics.pdf
Technical Notes & Articles | https://www.st.com/resource/en/technical_note/tn1489-security-bulletin-tn1489stpsirt-physical-attacks-on-stm32-and-stm32cube-firmware-stmicroelectronics.pdf

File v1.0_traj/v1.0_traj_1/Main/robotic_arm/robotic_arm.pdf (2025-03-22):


19/03/2025

robotic_arm Project
Configuration Report

## 1. Description

### 1.1. Project

Project Name | robotic_arm
Board Name | NUCLEO-F446RE
Generated with: | STM32CubeMX 6.12.1
Date | 03/19/2025

### 1.2. MCU

MCU Series | STM32F4
MCU Line | STM32F446
MCU name | STM32F446RETx
MCU Package | LQFP64
MCU Pin number | 64

### 1.3. Core(s) information

Core(s) | Arm Cortex-M4

## 2. Pinout Configuration

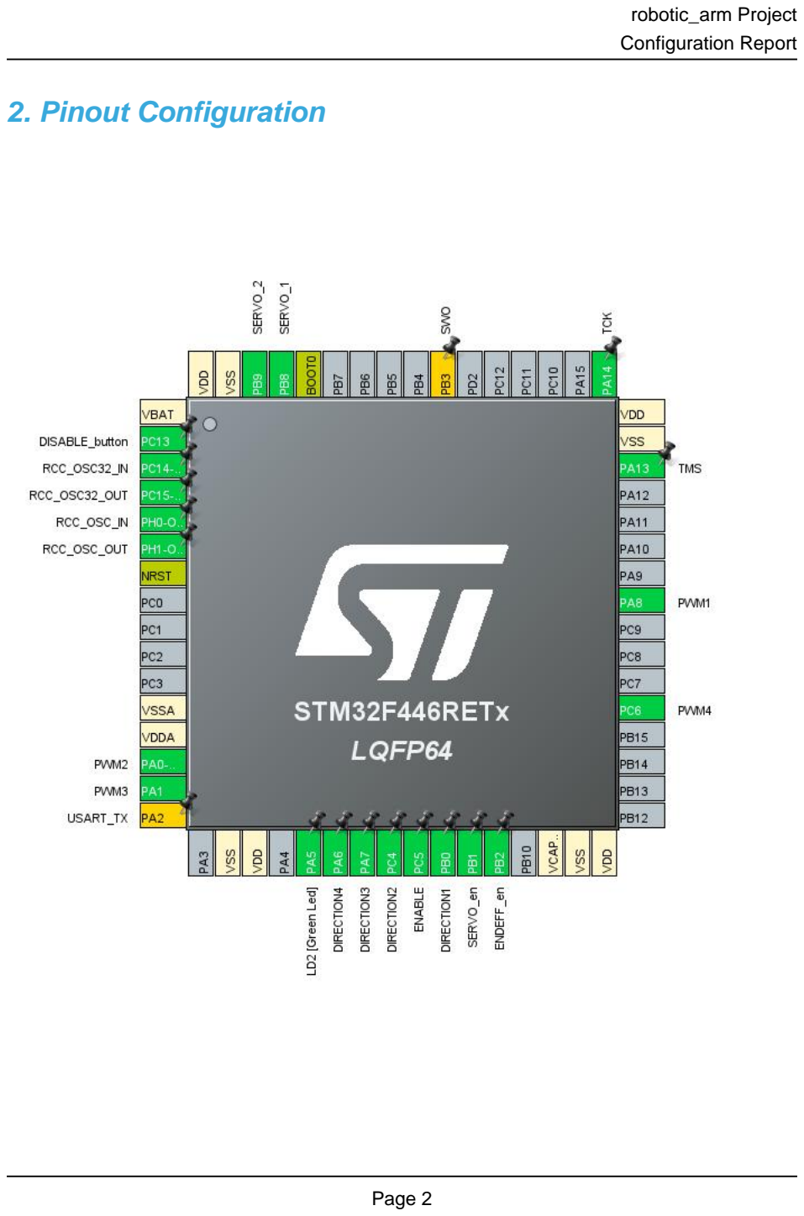
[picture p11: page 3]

## 3. Pins Configuration

Pin Number LQFP64 | Pin Name (function after reset) | Pin Type | Alternate Function(s) | Label
1 | VBAT | Power
2 | PC13 | I/O | GPIO_EXTI13 | DISABLE_button
3 | PC14-OSC32_IN | I/O | RCC_OSC32_IN
4 | PC15-OSC32_OUT | I/O | RCC_OSC32_OUT
5 | PH0-OSC_IN | I/O | RCC_OSC_IN
6 | PH1-OSC_OUT | I/O | RCC_OSC_OUT
7 | NRST | Reset
12 | VSSA | Power
13 | VDDA | Power
14 | PA0-WKUP | I/O | TIM2_CH1 | PWM2
15 | PA1 | I/O | TIM2_CH2 | PWM3
16 | PA2 * | I/O | USART2_TX | USART_TX
18 | VSS | Power
19 | VDD | Power
21 | PA5 ** | I/O | GPIO_Output | LD2 [Green Led]
22 | PA6 ** | I/O | GPIO_Output | DIRECTION4
23 | PA7 ** | I/O | GPIO_Output | DIRECTION3
24 | PC4 ** | I/O | GPIO_Output | DIRECTION2
25 | PC5 ** | I/O | GPIO_Output | ENABLE
26 | PB0 ** | I/O | GPIO_Output | DIRECTION1
27 | PB1 ** | I/O | GPIO_Output | SERVO_en
28 | PB2 ** | I/O | GPIO_Output | ENDEFF_en
30 | VCAP_1 | Power
31 | VSS | Power
32 | VDD | Power
37 | PC6 | I/O | TIM8_CH1 | PWM4
41 | PA8 | I/O | TIM1_CH1 | PWM1
46 | PA13 | I/O | SYS_JTMS-SWDIO | TMS
47 | VSS | Power
48 | VDD | Power
49 | PA14 | I/O | SYS_JTCK-SWCLK | TCK
55 | PB3 * | I/O | SYS_JTDO-SWO | SWO
60 | BOOT0 | Boot
61 | PB8 | I/O | TIM10_CH1 | SERVO_1
62 | PB9 | I/O | TIM11_CH1 | SERVO_2
63 | VSS | Power

Pin Number LQFP64 | Pin Name (function after reset) | Pin Type | Alternate Function(s) | Label
64 | VDD | Power

** The pin is affected with an I/O function
* The pin is affected with a peripheral function but no peripheral mode is activated

## 4. Clock Tree Configuration

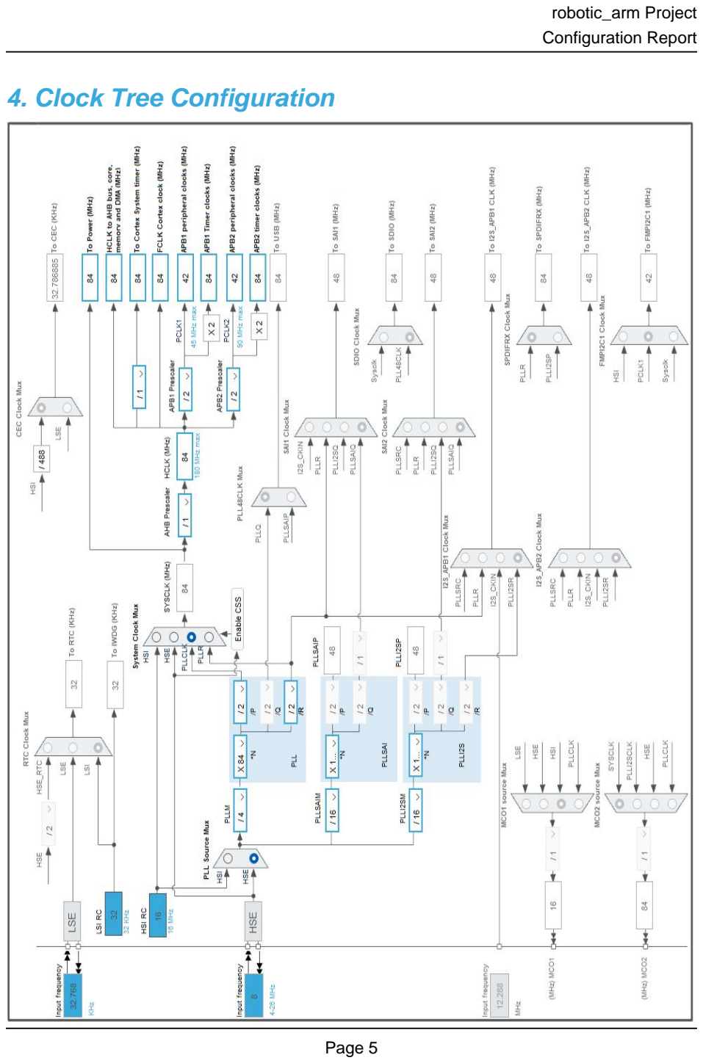
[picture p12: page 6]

## 1. Power Consumption Calculator report

### 1.1. Microcontroller Selection

Series | STM32F4
Line | STM32F446
MCU | STM32F446RETx
Datasheet | DS10693_Rev6

### 1.2. Parameter Selection

Temperature | 25
Vdd | 3.3

### 1.3. Battery Selection

Battery | Li-SOCL2(A3400)
Capacity | 3400.0 mAh
Self Discharge | 0.08 %/month
Nominal Voltage | 3.6 V
Max Cont Current | 100.0 mA
Max Pulse Current | 200.0 mA
Cells in series | 1
Cells in parallel | 1

### 1.4. Sequence

Step | Step1 | Step2
Mode | RUN | STOP_UDM (Under Drive)
Vdd | 3.3 | 3.3
Voltage Source | Battery | Battery
Range | Scale1-High | No Scale
Fetch Type | RAM/FLASH/REGON/ART/P REFETCH | n/a
CPU Frequency | 180 MHz | 0 Hz
Clock Configuration | HSE PLL | Regulator_LP Flash-PwrDwn
Clock Source Frequency | 4 MHz | 0 Hz
Peripherals
Additional Cons. | 0 mA | 0 mA
Average Current | 46 mA | 55 µA
Duration | 0.1 ms | 0.9 ms
DMIPS | 225.0 | 0.0
Ta Max | 98.02 | 104.99
Category | In DS Table | In DS Table

### 1.5. Results

Sequence Time | 1 ms | Average Current | 4.65 mA
Battery Life | 1 month | Average DMIPS | 225.0 DMIPS

### 1.6. Chart


## 2. Software Project

### 2.1. Project Settings

Name | Value
Project Name | robotic_arm
Project Folder | C:\Users\Francesco Stasi\OneDrive - Politecnico di
Toolchain / IDE | STM32CubeIDE
Firmware Package Name and Version | STM32Cube FW_F4 V1.28.1
Application Structure | Advanced
Generate Under Root | Yes
Do not generate the main() | No
Minimum Heap Size | 0x200
Minimum Stack Size | 0x400

### 2.2. Code Generation Settings

Name | Value
STM32Cube MCU packages and embedded software | Copy only the necessary library files
Generate peripheral initialization as a pair of '.c/.h' files | Yes
Backup previously generated files when re-generating | No
Keep User Code when re-generating | Yes
Delete previously generated files when not re-generated | Yes
Set all free pins as analog (to optimize the power consumption) | No
Enable Full Assert | No

### 2.3. Advanced Settings - Generated Function Calls

Rank | Function Name | Peripheral Instance Name
1 | SystemClock_Config | RCC
2 | MX_GPIO_Init | GPIO
3 | MX_TIM3_Init | TIM3
4 | MX_TIM5_Init | TIM5
5 | MX_TIM1_Init | TIM1
6 | MX_TIM2_Init | TIM2
7 | MX_TIM4_Init | TIM4
8 | MX_TIM8_Init | TIM8
9 | MX_TIM10_Init | TIM10
10 | MX_TIM11_Init | TIM11
11 | MX_TIM6_Init | TIM6

## 3. Peripherals and Middlewares Configuration

### 3.1. RCC

High Speed Clock (HSE): Crystal/Ceramic Resonator
Low Speed Clock (LSE) : Crystal/Ceramic Resonator
3.1.1. Parameter Settings:

System Parameters:

VDD voltage (V) | 3.3
Instruction Cache | Enabled
Prefetch Buffer | Enabled
Data Cache | Enabled
Flash Latency(WS) | 2 WS (3 CPU cycle)
RCC Parameters:
HSI Calibration Value | 16
TIM Prescaler Selection | Disabled
HSE Startup Timout Value (ms) | 100
LSE Startup Timout Value (ms) | 5000
Power Parameters:
Power Regulator Voltage Scale | Power Regulator Voltage Scale 3
Power Over Drive | Disabled

### 3.2. SYS

Debug: Serial Wire
Timebase Source: SysTick

### 3.3. TIM1

Clock Source : Internal Clock Channel1: PWM Generation CH1
3.3.1. Parameter Settings:

Counter Settings:

Prescaler (PSC - 16 bits value) | 4 *
Counter Mode | Up
Counter Period (AutoReload Register - 16 bits value ) | 65535
Internal Clock Division (CKD) | No Division
Repetition Counter (RCR - 8 bits value) | 0
auto-reload preload | Enable *

Trigger Output (TRGO) Parameters:
Master/Slave Mode (MSM bit) | Enable (Trigger delayed for master/slaves simultaneous start) *
Trigger Event Selection | Update Event *
Break And Dead Time management - BRK Configuration:
BRK State | Disable
BRK Polarity | High
Break And Dead Time management - Output Configuration:
Automatic Output State | Disable
Off State Selection for Run Mode (OSSR) | Disable
Off State Selection for Idle Mode (OSSI) | Disable
Lock Configuration | Off
PWM Generation Channel 1:
Mode | PWM mode 1
Pulse (16 bits value) | 32768 *
Output compare preload | Enable
Fast Mode | Enable *
CH Polarity | High
CH Idle State | Reset

### 3.4. TIM2

Clock Source : Internal Clock Channel1: PWM Generation CH1 Channel2: PWM Generation CH2
3.4.1. Parameter Settings:

Counter Settings:

Prescaler (PSC - 16 bits value) | 4 *
Counter Mode | Up
Counter Period (AutoReload Register - 32 bits value ) | 65535 *
Internal Clock Division (CKD) | No Division
auto-reload preload | Enable *
Trigger Output (TRGO) Parameters:
Master/Slave Mode (MSM bit) | Enable (Trigger delayed for master/slaves simultaneous start) *
Trigger Event Selection | Update Event *
PWM Generation Channel 1:

Mode | PWM mode 1
Pulse (32 bits value) | 32768 *
Output compare preload | Enable
Fast Mode | Enable *
CH Polarity | High
PWM Generation Channel 2:
Mode | PWM mode 1
Pulse (32 bits value) | 32768 *
Output compare preload | Enable
Fast Mode | Enable *
CH Polarity | High

### 3.5. TIM3

Slave Mode: Trigger Mode
Trigger Source: ITR1
Clock Source : Internal Clock
3.5.1. Parameter Settings:

Counter Settings:

Prescaler (PSC - 16 bits value) | 65535 *
Counter Mode | Up
Counter Period (AutoReload Register - 16 bits value ) | 199 *
Internal Clock Division (CKD) | No Division
auto-reload preload | Enable *
Slave Mode Controller | Trigger Mode
Trigger Output (TRGO) Parameters:
Master/Slave Mode (MSM bit) | Disable (Trigger input effect not delayed)
Trigger Event Selection | Reset (UG bit from TIMx_EGR)

### 3.6. TIM4

Slave Mode: Trigger Mode
Trigger Source: ITR0
mode: Clock Source
3.6.1. Parameter Settings:

Counter Settings:

Prescaler (PSC - 16 bits value) | 65535 *
Counter Mode | Up
Counter Period (AutoReload Register - 16 bits value ) | 199 *
Internal Clock Division (CKD) | No Division
auto-reload preload | Enable *
Slave Mode Controller | Trigger Mode
Trigger Output (TRGO) Parameters:
Master/Slave Mode (MSM bit) | Disable (Trigger input effect not delayed)
Trigger Event Selection | Reset (UG bit from TIMx_EGR)

### 3.7. TIM5

Slave Mode: Trigger Mode
Trigger Source: ITR3
mode: Clock Source
3.7.1. Parameter Settings:

Counter Settings:

Prescaler (PSC - 16 bits value) | 65535 *
Counter Mode | Up
Counter Period (AutoReload Register - 32 bits value ) | 199 *
Internal Clock Division (CKD) | No Division
auto-reload preload | Disable
Slave Mode Controller | Trigger Mode
Trigger Output (TRGO) Parameters:
Master/Slave Mode (MSM bit) | Disable (Trigger input effect not delayed)
Trigger Event Selection | Reset (UG bit from TIMx_EGR)

### 3.8. TIM6

mode: Activated
3.8.1. Parameter Settings:

Counter Settings:

Prescaler (PSC - 16 bits value) | 1400*3 *
Counter Mode | Up
Counter Period (AutoReload Register - 16 bits value ) | 59999 *
auto-reload preload | Disable

Trigger Output (TRGO) Parameters:

Trigger Event Selection | Reset (UG bit from TIMx_EGR)

### 3.9. TIM8

Clock Source : Internal Clock
Channel1: PWM Generation CH1
3.9.1. Parameter Settings:

Counter Settings:

Prescaler (PSC - 16 bits value) | 4 *
Counter Mode | Up
Counter Period (AutoReload Register - 16 bits value ) | 65535
Internal Clock Division (CKD) | No Division
Repetition Counter (RCR - 8 bits value) | 0
auto-reload preload | Enable *
Trigger Output (TRGO) Parameters:
Master/Slave Mode (MSM bit) | Enable (Trigger delayed for master/slaves simultaneous start) *
Trigger Event Selection | Update Event *
Break And Dead Time management - BRK Configuration:
BRK State | Disable
BRK Polarity | High
Break And Dead Time management - Output Configuration:
Automatic Output State | Disable
Off State Selection for Run Mode (OSSR) | Disable
Off State Selection for Idle Mode (OSSI) | Disable
Lock Configuration | Off
PWM Generation Channel 1:
Mode | PWM mode 1
Pulse (16 bits value) | 32768 *
Output compare preload | Enable
Fast Mode | Enable *
CH Polarity | High
CH Idle State | Reset

### 3.10. TIM10

mode: Activated
Channel1: PWM Generation CH1
3.10.1. Parameter Settings:

Counter Settings:

Prescaler (PSC - 16 bits value) | 0
Counter Mode | Up
Counter Period (AutoReload Register - 16 bits value ) | 65535
Internal Clock Division (CKD) | No Division
auto-reload preload | Enable *
PWM Generation Channel 1:
Mode | PWM mode 1
Pulse (16 bits value) | 1 *
Output compare preload | Enable
Fast Mode | Enable *
CH Polarity | High

### 3.11. TIM11

mode: Activated
Channel1: PWM Generation CH1
3.11.1. Parameter Settings:

Counter Settings:

Prescaler (PSC - 16 bits value) | 0
Counter Mode | Up
Counter Period (AutoReload Register - 16 bits value ) | 65535
Internal Clock Division (CKD) | No Division
auto-reload preload | Enable *
PWM Generation Channel 1:
Mode | PWM mode 1
Pulse (16 bits value) | 1 *
Output compare preload | Enable
Fast Mode | Enable *
CH Polarity | High

* User modified value

## 4. System Configuration

### 4.1. GPIO configuration

IP | Pin | Signal | GPIO mode | GPIO pull/up pull down | Max Speed | User Label
RCC | PC14-OSC32_IN | RCC_OSC32_IN | n/a | n/a | n/a
| PC15-OSC32_OU T | RCC_OSC32_O UT | n/a | n/a | n/a
| PH0-OSC_IN | RCC_OSC_IN | n/a | n/a | n/a
| PH1-OSC_OUT | RCC_OSC_OUT | n/a | n/a | n/a
SYS | PA13 | SYS_JTMS-SWDIO | n/a | n/a | n/a | TMS
| PA14 | SYS_JTCK-SWCLK | n/a | n/a | n/a | TCK
TIM1 | PA8 | TIM1_CH1 | Alternate Function Push Pull | No pull-up and no pull-down | Low | PWM1
TIM2 | PA0-WKUP | TIM2_CH1 | Alternate Function Push Pull | No pull-up and no pull-down | Low | PWM2
| PA1 | TIM2_CH2 | Alternate Function Push Pull | No pull-up and no pull-down | Low | PWM3
TIM8 | PC6 | TIM8_CH1 | Alternate Function Push Pull | No pull-up and no pull-down | Low | PWM4
TIM10 | PB8 | TIM10_CH1 | Alternate Function Push Pull | No pull-up and no pull-down | Low | SERVO_1
TIM11 | PB9 | TIM11_CH1 | Alternate Function Push Pull | No pull-up and no pull-down | Low | SERVO_2
Single Mapped Signals | PA2 | USART2_TX | Alternate Function Push Pull | No pull-up and no pull-down | Very High * | USART_TX
| PB3 | SYS_JTDO-SWO | n/a | n/a | n/a | SWO
GPIO | PC13 | GPIO_EXTI13 | External Interrupt Mode with Rising edge trigger detection | No pull-up and no pull-down | n/a | DISABLE_button
| PA5 | GPIO_Output | Output Push Pull | No pull-up and no pull-down | Low | LD2 [Green Led]
| PA6 | GPIO_Output | Output Push Pull | Pull-down * | Low | DIRECTION4
| PA7 | GPIO_Output | Output Push Pull | Pull-down * | Low | DIRECTION3
| PC4 | GPIO_Output | Output Push Pull | Pull-down * | Low | DIRECTION2
| PC5 | GPIO_Output | Output Push Pull | Pull-up * | High * | ENABLE
| PB0 | GPIO_Output | Output Push Pull | Pull-down * | Low | DIRECTION1
| PB1 | GPIO_Output | Output Push Pull | Pull-down * | Low | SERVO_en
| PB2 | GPIO_Output | Output Push Pull | Pull-up * | Low | ENDEFF_en

### 4.2. DMA configuration

nothing configured in DMA service

### 4.3. NVIC configuration

4.3.1. NVIC
Interrupt Table | Enable | Preenmption Priority | SubPriority
Non maskable interrupt | true | 0 | 0
Hard fault interrupt | true | 0 | 0
Memory management fault | true | 0 | 0
Pre-fetch fault, memory access fault | true | 0 | 0
Undefined instruction or illegal state | true | 0 | 0
System service call via SWI instruction | true | 0 | 0
Debug monitor | true | 0 | 0
Pendable request for system service | true | 0 | 0
System tick timer | true | 0 | 0
TIM1 trigger and commutation interrupts and TIM11 global interrupt | true | 1 | 0
TIM1 capture compare interrupt | true | 1 | 0
TIM2 global interrupt | true | 1 | 0
EXTI line[15:10] interrupts | true | 0 | 0
TIM8 break interrupt and TIM12 global interrupt | true | 1 | 0
TIM8 update interrupt and TIM13 global interrupt | true | 1 | 0
TIM8 trigger and commutation interrupts and TIM14 global interrupt | true | 1 | 0
TIM8 capture compare interrupt | true | 1 | 0
TIM6 global interrupt and DAC1, DAC2 underrun error interrupts | true | 1 | 0
PVD interrupt through EXTI line 16 | | unused
Flash global interrupt | | unused
RCC global interrupt | | unused
TIM1 break interrupt and TIM9 global interrupt | | unused
TIM1 update interrupt and TIM10 global interrupt | | unused
TIM3 global interrupt | | unused
TIM4 global interrupt | | unused
TIM5 global interrupt | | unused
FPU global interrupt | | unused
4.3.2. NVIC Code generation

Enabled interrupt Table Select for init
sequence ordering
| | Generate IRQ
| | handler | Call HAL handler
Non maskable interrupt | false | true | false
Hard fault interrupt | false | true | false

Enabled interrupt Table | Select for init sequence ordering | Generate IRQ handler | Call HAL handler
Memory management fault | false | true | false
Pre-fetch fault, memory access fault | false | true | false
Undefined instruction or illegal state | false | true | false
System service call via SWI instruction | false | true | false
Debug monitor | false | true | false
Pendable request for system service | false | true | false
System tick timer | false | true | true
TIM1 trigger and commutation interrupts and TIM11 global interrupt | false | true | true
TIM1 capture compare interrupt | false | true | true
TIM2 global interrupt | false | true | true
EXTI line[15:10] interrupts | false | true | true
TIM8 break interrupt and TIM12 global interrupt | false | true | true
TIM8 update interrupt and TIM13 global interrupt | false | true | true
TIM8 trigger and commutation interrupts and TIM14 global interrupt | false | true | true
TIM8 capture compare interrupt | false | true | true
TIM6 global interrupt and DAC1, DAC2 underrun error interrupts | false | true | true

* User modified value

## 5. System Views

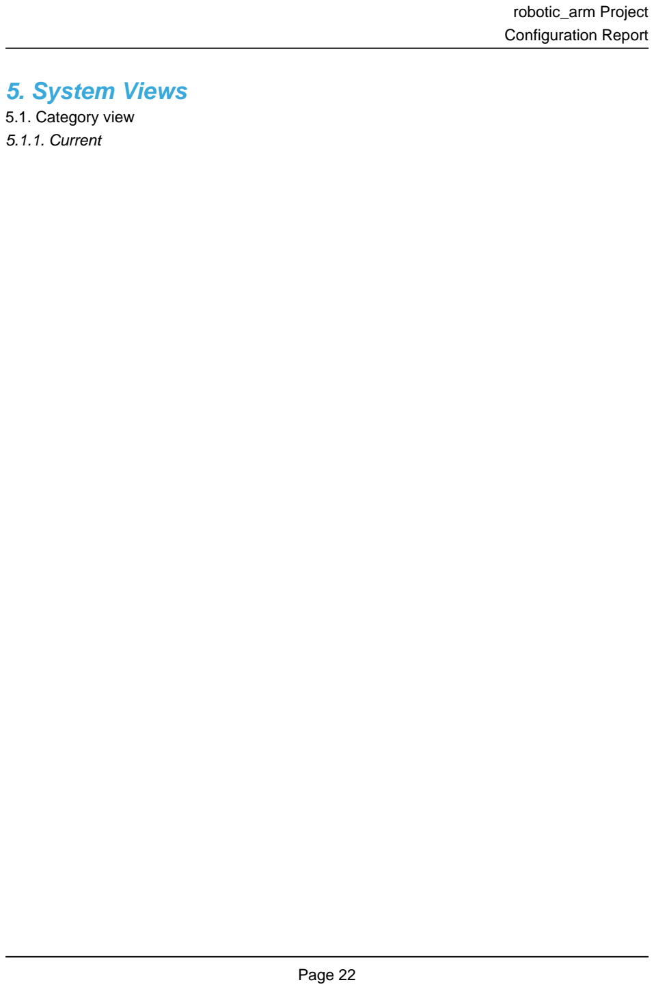
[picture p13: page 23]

5.1. Category view
5.1.1. Current

## 6. Docs & Resources

Type | Link
BSDL files | https://www.st.com/resource/en/bsdl_model/stm32f446_bsdl.zip
IBIS models | https://www.st.com/resource/en/ibis_model/stm32f446_ibis.zip
System View Description | https://www.st.com/resource/en/svd/stm32f4-svd.zip
Presentations | https://www.st.com/resource/en/product_presentation/stm32-stm8_embedded_software_solutions.pdf
Presentations | https://www.st.com/resource/en/product_presentation/stm32_eval-tools_portfolio.pdf
Presentations | https://www.st.com/resource/en/product_presentation/stm32_stm8_functi onal-safety-packages.pdf
Presentations | https://www.st.com/resource/en/product_presentation/stm32-stm8_software_development_tools.pdf
Presentations | https://www.st.com/resource/en/product_presentation/microcontrollers-stm32-family-overview.pdf
Brochures | https://www.st.com/resource/en/brochure/products-and-solutions-for-plcs-and-smart-i-os.pdf
Flyers | https://www.st.com/resource/en/flyer/flstm32nucleo.pdf
Flyers | https://www.st.com/resource/en/flyer/flstm32trust.pdf
Product Certifications | https://www.st.com/resource/en/certification_document/stm32_authentication_can.pdf
Application Notes | https://www.st.com/resource/en/application_note/an1709-emc-design-guide-for-stm8-stm32-and-legacy-mcus-stmicroelectronics.pdf
Application Notes | https://www.st.com/resource/en/application_note/an2606-stm32-microcontroller-system-memory-boot-mode-stmicroelectronics.pdf
Application Notes | https://www.st.com/resource/en/application_note/an2945-stm8s-and-stm32-mcus-a-consistent-832bit-product-line-for-painless-migration-stmicroelectronics.pdf
Application Notes | https://www.st.com/resource/en/application_note/an3070-managing-the- driver-enable-signal-for-rs485-and-iolink-communications-with-the-

| stm32s-usart-stmicroelectronics.pdf
Application Notes | https://www.st.com/resource/en/application_note/an3126-audio-and-waveform-generation-using-the-dac-in-stm32-products-stmicroelectronics.pdf
Application Notes | https://www.st.com/resource/en/application_note/an3154-can-protocol-used-in-the-stm32-bootloader-stmicroelectronics.pdf
Application Notes | https://www.st.com/resource/en/application_note/an3155-usart-protocol-used-in-the-stm32-bootloader-stmicroelectronics.pdf
Application Notes | https://www.st.com/resource/en/application_note/an3156-usb-dfu-protocol-used-in-the-stm32-bootloader-stmicroelectronics.pdf
Application Notes | https://www.st.com/resource/en/application_note/an3364-migration-and-compatibility-guidelines-for-stm32-microcontroller-applications-stmicroelectronics.pdf
Application Notes | https://www.st.com/resource/en/application_note/an3997-audio-playback-and-recording-using-the-stm32f4discovery-stmicroelectronics.pdf
Application Notes | https://www.st.com/resource/en/application_note/an3998-pdm-audio-software-decoding-on-stm32-microcontrollers-stmicroelectronics.pdf
Application Notes | https://www.st.com/resource/en/application_note/an4031-using-the-stm32f2-stm32f4-and-stm32f7-series-dma-controller-stmicroelectronics.pdf
Application Notes | https://www.st.com/resource/en/application_note/an4221-i2c-protocol-used-in-the-stm32-bootloader-stmicroelectronics.pdf
Application Notes | https://www.st.com/resource/en/application_note/an4286-spi-protocol-used-in-the-stm32-bootloader-stmicroelectronics.pdf
Application Notes | https://www.st.com/resource/en/application_note/an4488-getting-started-with-stm32f4xxxx-mcu-hardware-development-stmicroelectronics.pdf
Application Notes | https://www.st.com/resource/en/application_note/an4566-extending-the-dac-performance-of-stm32-microcontrollers-stmicroelectronics.pdf
Application Notes | https://www.st.com/resource/en/application_note/an4640-peripherals-interconnections-on-stm32f4057xx-stm32f4157xx-stm32f42xxx-stm32f43xxx-stm32f446xx-and-stm32f469479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
Application Notes | https://www.st.com/resource/en/application_note/an4655-virtually- increasing-the-number-of-serial-communication-peripherals-in-stm32-

| applications-stmicroelectronics.pdf
Application Notes | https://www.st.com/resource/en/application_note/an4658-migration-of-applications-from-stm32f429439-lines-to-stm32f446-line-stmicroelectronics.pdf
Application Notes | https://www.st.com/resource/en/application_note/an4739-stm32cube-firmware-examples-for-stm32f4-series-stmicroelectronics.pdf
Application Notes | https://www.st.com/resource/en/application_note/an4750-handling-of-soft-errors-in-stm32-applications-stmicroelectronics.pdf
Application Notes | https://www.st.com/resource/en/application_note/an4776-generalpurpose-timer-cookbook-for-stm32-microcontrollers-stmicroelectronics.pdf
Application Notes | https://www.st.com/resource/en/application_note/an4803-highspeed-si-simulations-using-ibis-and-boardlevel-simulations-using-hyperlynx-si-on-stm32-mcus-and-mpus-stmic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
Application Notes | https://www.st.com/resource/en/application_note/an4850-stm32-mcus-spreadspectrum-clock-generation-principles-properties-and-implementation-stmicroelectronics.pdf
Application Notes | https://www.st.com/resource/en/application_note/an4989-stm32-microcontroller-debug-toolbox-stmicroelectronics.pdf
Application Notes | https://www.st.com/resource/en/application_note/an4995-using-an-electromyogram-technique-to-detect-muscle-activity-stmicroelectronics.pdf
Application Notes | https://www.st.com/resource/en/application_note/an5027-interfacing-pdm-digital-microphones-using-stm32-mcus-and-mpus-stmicroelectronics.pdf
Application Notes | https://www.st.com/resource/en/application_note/an5073-receiving-spdif-audio-stream-with-the-stm32f4f7h7-series-stmicroelectronics.pdf
Application Notes | https://www.st.com/resource/en/application_note/an4760-quadspi-interface-on-stm32-microcontrollers-and-microprocessors--stmicroelectronics.pdf
Application Notes | https://www.st.com/resource/en/application_note/an4899-stm32-microcontroller-gpio-hardware-settings-and-lowpower-consumption-stmicroelectronics.pdf
Application Notes | https://www.st.com/resource/en/application_note/an5612-esd-protection-of-stm32-mcus-and-mpus-stmicroelectronics.pdf

Application Notes | https://www.st.com/resource/en/application_note/an4838-introduction-to-memory-protection-unit-management-on-stm32-mcus-stmicroelectronics.pdf
Application Notes | https://www.st.com/resource/en/application_note/an4879-introduction-to-usb-hardware-and-pcb-guidelines-using-stm32-mcus-stmicroelectronics.pdf
Application Notes | https://www.st.com/resource/en/application_note/an5225-introduction-to-usb-typec-power-delivery-for-stm32-mcus-and-mpus-stmicroelectronics.pdf
Application Notes | https://www.st.com/resource/en/application_note/an5537-how-to-use-adc-oversampling-techniques-to-improve-signaltonoise-ratio-on-stm32-mcus-stmicroelectronics.pdf
Application Notes | https://www.st.com/resource/en/application_note/an5036-guidelines-for-thermal-management-on-stm32-applications-stmicroelectronics.pdf
Application Notes | https://www.st.com/resource/en/application_note/an4230-introduction-to-random-number-generation-validation-using-the-nist-statistical-test-suite-for-stm32-mcus-and-m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
Application Notes | https://www.st.com/resource/en/application_note/an2867-guidelines-for-oscillator-design-on-stm8afals-and-stm32-mcusmpus-stmicroelectronics.pdf
Application Notes | https://www.st.com/resource/en/application_note/an4013-introduction-to-timers-for-stm32-mcus-stmicroelectronics.pdf
Application Notes | https://www.st.com/resource/en/application_note/an4277-how-to-use-pwm-shutdown-for-motor-control-and-digital-power-conversion-on-stm32-mcus-stmicroelectronics.pdf
Application Notes | https://www.st.com/resource/en/application_note/an4759-introduction-to-using-the-hardware-realtime-clock-rtc-and-the-tamper-management-unit-tamp-with-stm32-mcus-stmi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
Application Notes | https://www.st.com/resource/en/application_note/an4908-getting-started-with-usart-automatic-baud-rater-detection-for-stm32-mcus-stmicroelectronics.pdf
Application Notes | https://www.st.com/resource/en/application_note/an5156-introduction-to-security-for-stm32-mcus-stmicroelectronics.pdf
Application Notes | https://www.st.com/resource/en/application_note/an5543-guidelines-for-

| enhanced-spi-communication-on-stm32-mcus-and-mpus-stmicroelectronics.pdf
Application Notes | https://www.st.com/resource/en/application_note/an5992-migrating-from-stm32f446-to-stm32h523533-mcus-stmicroelectronics.pdf
Application Notes | https://www.st.com/resource/en/application_note/cd00211314-how-to-optimize-the-adc-accuracy-in-the-stm32-mcus-stmicroelectronics.pdf
Application Notes | https://www.st.com/resource/en/application_note/an2639-soldering-recommendations-and-package-information-for-leadfree-ecopack2-mcus-and-mpus-stmicroelectronics.pdf
Application Notes | https://www.st.com/resource/en/application_note/an5020-introduction-to-digital-camera-interface-dcmi-for-stm32-mcus-stmicroelectronics.pdf
Application Notes for related Tools & Software | https://www.st.com/resource/en/application_note/an2656-stm32f10xxx-lcd-glass-driver-firmware-stmicroelectronics.pdf
Application Notes for related Tools & Software | https://www.st.com/resource/en/application_note/an2790-tft-lcd-interfacing-with-the-highdensity-stm32f10xxx-fsmc-stmicroelectronics.pdf
Application Notes for related Tools & Software | https://www.st.com/resource/en/application_note/an3078-stm32-inapplication-programming-over-the-ic-bus-stmicroelectronics.pdf
Application Notes for related Tools & Software | https://www.st.com/resource/en/application_note/an3116-stm32s-adc-modes-and-their-applications-stmicroelectronics.pdf
Application Notes for related Tools & Software | https://www.st.com/resource/en/application_note/an3174-implementing-receivers-for-infrared-remote-control-protocols-using-stm32f10xxx-microcontrollers-stmicroelectro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
Application Notes for related Tools & Software | https://www.st.com/resource/en/application_note/an3241-qvga-tftlcd-direct-drive-using-the-stm32f10xx-fsmc-peripheral-stmicroelectronics.pdf
Application Notes for related Tools & Software | https://www.st.com/resource/en/application_note/an3307-guidelines-for-obtaining-iec-60335-class-b-certification-for-any-stm32-application-stmicroelectronics.pdf

Application Notes
for related Tools

https://www.st.com/resource/en/application_note/an3965-stm32f40xstm32f41x-inapplication-programming-using-the-usart-

& Software | stmicroelectronics.pdf
Application Notes for related Tools & Software | https://www.st.com/resource/en/application_note/an3969-eeprom-emulation-in-stm32f40xstm32f41x-microcontrollers-stmicroelectronics.pdf
Application Notes for related Tools & Software | https://www.st.com/resource/en/application_note/an4044-floating-point-unit-demonstration-on-stm32-microcontrollers-stmicroelectronics.pdf
Application Notes for related Tools & Software | https://www.st.com/resource/en/application_note/an4323-getting-started-with-stemwin-library-stmicroelectronics.pdf
Application Notes for related Tools & Software | https://www.st.com/resource/en/application_note/an4365-using-stm32f4-mcu-power-modes-with-best-dynamic-efficiency-stmicroelectronics.pdf
Application Notes for related Tools & Software | https://www.st.com/resource/en/application_note/an4435-guidelines-for-obtaining-ulcsaiec-607301603351-class-b-certification-in-any-stm32-application-stmicroelectroni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
Application Notes for related Tools & Software | https://www.st.com/resource/en/application_note/an4457-implementing-an-emulated-uart-on-stm32f4-microcontrollers-stmicroelectronics.pdf
Application Notes for related Tools & Software | https://www.st.com/resource/en/application_note/an4499-stm32--nrf51822-bluetooth-low-energy-system-solution-stmicroelectronics.pdf
Application Notes for related Tools & Software | https://www.st.com/resource/en/application_note/an4657-stm32-inapplication-programming-iap-using-the-usart-stmicroelectronics.pdf
Application Notes for related Tools & Software | https://www.st.com/resource/en/application_note/an4666-parallel-synchronous-transmission-using-gpio-and-dma-stmicroelectronics.pdf
Application Notes for related Tools & Software | https://www.st.com/resource/en/application_note/an4678-full-duplex-spi-emulation-for-stm32f4-microcontrollers-stmicroelectronics.pdf
Application Notes for related Tools & Software | https://www.st.com/resource/en/application_note/an4701-proprietary-code-readout-protection-on-microcontrollers-of-the-stm32f4-series-stmicroelectronics.pdf

Application Notes for related Tools & Software | https://www.st.com/resource/en/application_note/an4739-stm32cube-firmware-examples-for-stm32f4-series-stmicroelectronics.pdf
Application Notes for related Tools & Software | https://www.st.com/resource/en/application_note/an4758-proprietary-code-readout-protection-on-stm32l4-stm32l4-stm32g4-and-stm32wb-series-mcus-stmicroelectronics.pdf
Application Notes for related Tools & Software | https://www.st.com/resource/en/application_note/an4841-digital-signal-processing-for-stm32-microcontrollers-using-cmsis-stmicroelectronics.pdf
Application Notes for related Tools & Software | https://www.st.com/resource/en/application_note/an4852-programming-an-external-flash-memory-using-the-uart-bootloader-builtin-stm32-microcontrollers-stmicroelectroni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
Application Notes for related Tools & Software | https://www.st.com/resource/en/application_note/an4968-proprietary-code-read-out-protection-pcrop-on-stm32f72xxx-and-stm32f73xxx-microcontrollers-stmicroelectronics.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
Application Notes for related Tools & Software | https://www.st.com/resource/en/application_note/an5056-integration-guide-for-the-xcubesbsfu-stm32cube-expansion-package-stmicroelectronics.pdf
Application Notes for related Tools & Software | https://www.st.com/resource/en/application_note/an5360-getting-started-with-projects-based-on-the-stm32mp1-series-in-stm32cubeide-stmicroelectronics.pdf
Application Notes for related Tools & Software | https://www.st.com/resource/en/application_note/an5361-getting-started-with-projects-based-on-dualcore-stm32h7-microcontrollers-in-stm32cubeide-stmicroelectronics.pd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
Application Notes for related Tools & Software | https://www.st.com/resource/en/application_note/an5394-getting-started-with-projects-based-on-the-stm32l5-series-in-stm32cubeide-stmicroelectronics.pdf
Application Notes for related Tools & Software | https://www.st.com/resource/en/application_note/an5418-how-to-build-a-simple-usbpd-sink-application-with-stm32cubemx-stmicroelectronics.pdf
Application Notes for related Tools & Software | https://www.st.com/resource/en/application_note/an5426-migrating-graphics-middleware-projects-from-stm32cubemx-540-to-stm32cubemx-550-stmicroelectronics.pdf
Application Notes | https://www.st.com/resource/en/application_note/an5464-position-control-

for related Tools & Software | of-a-threephase-permanent-magnet-motor-using-xcubemcsdk-or-xcubemcsdkful-stmicroelectronics.pdf
Application Notes for related Tools & Software | https://www.st.com/resource/en/application_note/an5564-getting-started-with-projects-based-on-dualcore-stm32wl-microcontrollers-in-stm32cubeide-stmicroelectronics.pd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
Application Notes for related Tools & Software | https://www.st.com/resource/en/application_note/an5698-adapting-the-xcubestl-functional-safety-package-for-stm32-iec-61508-compliant-to-other-safety-standards-stmicr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
Application Notes for related Tools & Software | https://www.st.com/resource/en/application_note/an5731-stm32cubemx-and-stm32cubeide-threadsafe-solution-stmicroelectronics.pdf
Application Notes for related Tools & Software | https://www.st.com/resource/en/application_note/an4502-stm32-smbuspmbus-expansion-package-for-stm32cube-stmicroelectronics.pdf
Application Notes for related Tools & Software | https://www.st.com/resource/en/application_note/an5952-how-to-use-cmake-in-stm32cubeide-stmicroelectronics.pdf
Application Notes for related Tools & Software | https://www.st.com/resource/en/application_note/an5054-how-to-perform-secure-programming-using-stm32cubeprogrammer-stmicroelectronics.pdf
Application Notes for related Tools & Software | https://www.st.com/resource/en/application_note/an6179-how-to-integrate-the-stl-firmware-into-a-time-critical-user-application-stmicroelectronics.pdf
Errata Sheets | https://www.st.com/resource/en/errata_sheet/es0298-stm32f446xcxe-device-errata-stmicroelectronics.pdf
Datasheet | https://www.st.com/resource/en/datasheet/dm00141306.pdf
Programming Manuals | https://www.st.com/resource/en/programming_manual/pm0214-stm32-cortexm4-mcus-and-mpus-programming-manual-stmicroelectronics.pdf
Reference Manuals | https://www.st.com/resource/en/reference_manual/rm0390-stm32f446xx-advanced-armbased-32bit-mcus-stmicroelectronics.pdf
Technical Notes & Articles | https://www.st.com/resource/en/technical_note/tn0516-overview-of-the-stm32f0xf100xxf103xx-and-stm32f2xxf30xf4xx-mcus-pmsm-singledual-foc-sdk-v40-stmicroelectronics.p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

Technical Notes & Articles | https://www.st.com/resource/en/technical_note/tn1163-description-of-wlcsp-for-microcontrollers-and-recommendations-for-its-use-stmicroelectronics.pdf
Technical Notes & Articles | https://www.st.com/resource/en/technical_note/tn1204-tape-and-reel-shipping-media-for-stm32-microcontrollers-in-bga-packages-stmicroelectronics.pdf
Technical Notes & Articles | https://www.st.com/resource/en/technical_note/tn1205-tape-and-reel-shipping-media-for-stm8-and-stm32-microcontrollers-in-fpn-packages-stmicroelectronics.pdf
Technical Notes & Articles | https://www.st.com/resource/en/technical_note/tn1206-tape-and-reel-shipping-media-for-stm8-and-stm32-microcontrollers-in-qfp-packages-stmicroelectronics.pdf
Technical Notes & Articles | https://www.st.com/resource/en/technical_note/tn1207-tape-and-reel-shipping-media-for-stm8-and-stm32-microcontrollers-in-so-packages-stmicroelectronics.pdf
Technical Notes & Articles | https://www.st.com/resource/en/technical_note/tn1208-tape-and-reel-shipping-media-for-stm8-and-stm32-microcontrollers-in-tssop-and-ssop-packages-stmicroelectronics.p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
Technical Notes & Articles | https://www.st.com/resource/en/technical_note/tn1433-reference-device-marking-schematics-for-stm32-microcontrollers-and-microprocessors-stmicroelectronics.pdf
Technical Notes & Articles | https://www.st.com/resource/en/technical_note/tn1489-security-bulletin-tn1489stpsirt-physical-attacks-on-stm32-and-stm32cube-firmware-stmicroelectronics.pdf

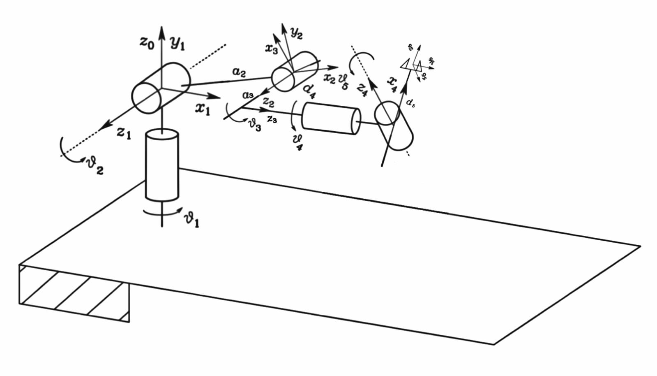
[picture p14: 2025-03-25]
media/report/robotic_arm_5dof.jpg

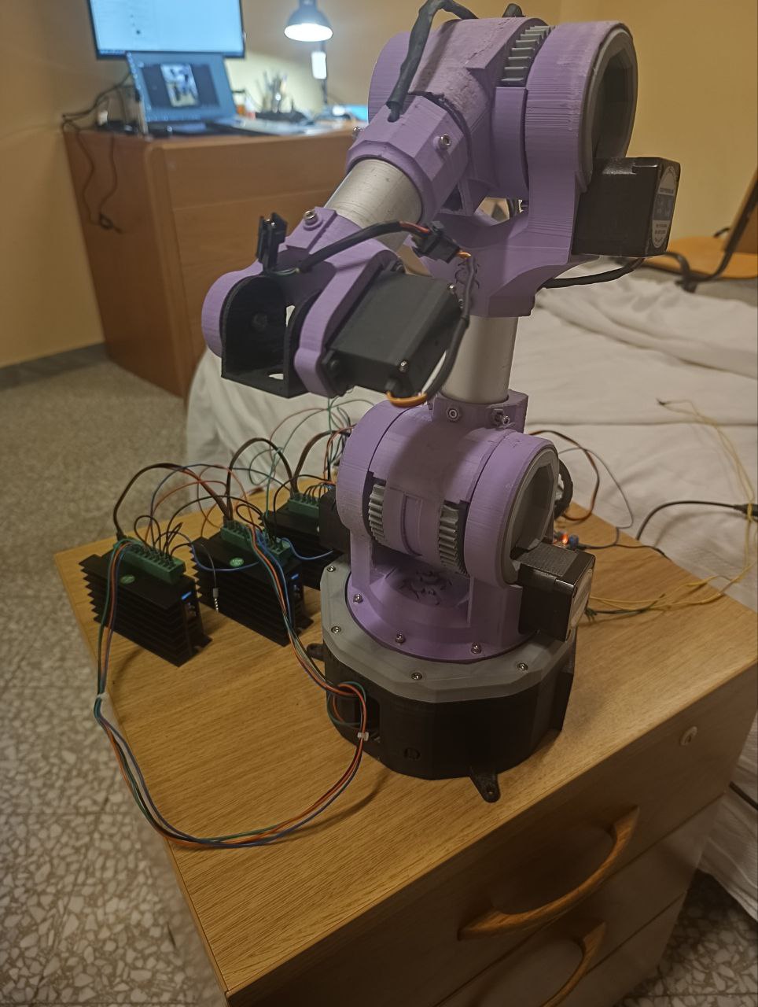
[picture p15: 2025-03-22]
media/rasn5_1.jpg

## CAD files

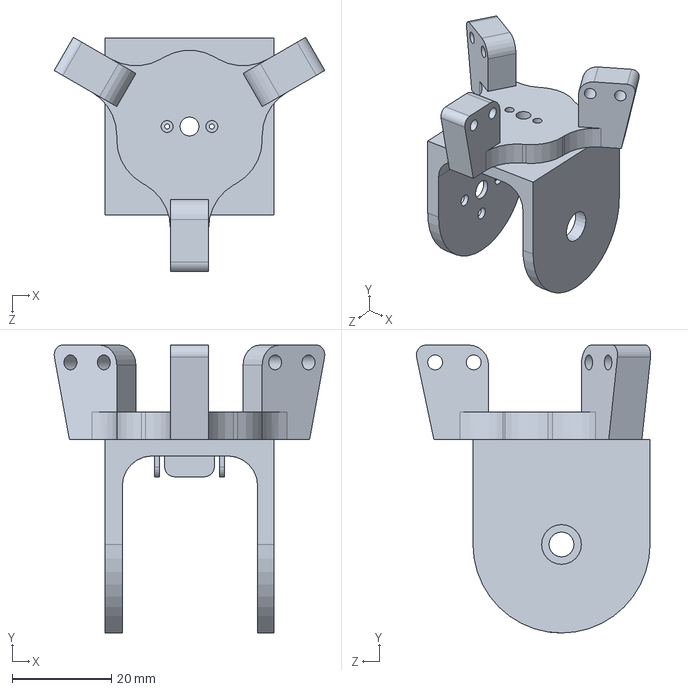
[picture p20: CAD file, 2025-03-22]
3d_model/endeffector_parts/end_ass.SLDASM
54.4 x 57.9 x 47.1 mm

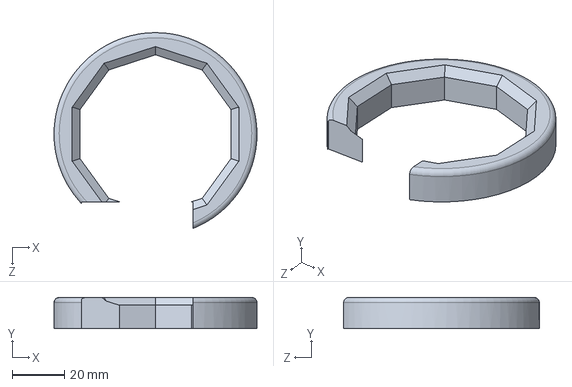
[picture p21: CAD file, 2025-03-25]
3d_model/additional parts/cover_sx_j2_2.SLDPRT
78.0 x 12.0 x 75.2 mm

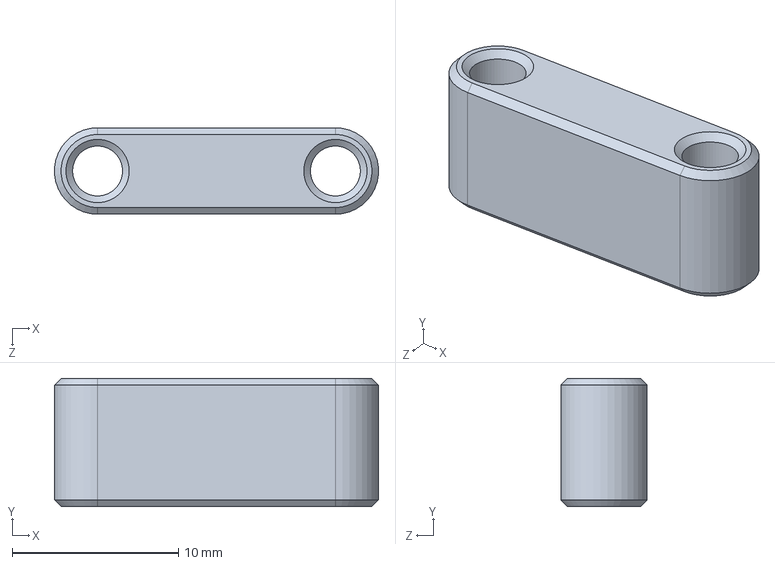
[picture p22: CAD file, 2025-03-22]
3d_model/endeffector_parts/Endeffector_adaptive_config-3f_1gdl/Connecting_rod_1_part.SLDPRT
19.5 x 7.70 x 5.20 mm

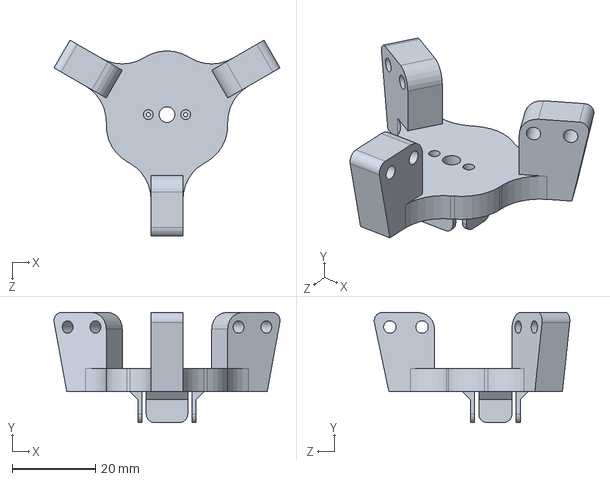
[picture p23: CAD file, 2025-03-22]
3d_model/endeffector_parts/Endeffector_static_config-3f/Base_part.SLDPRT
54.4 x 26.5 x 47.1 mm

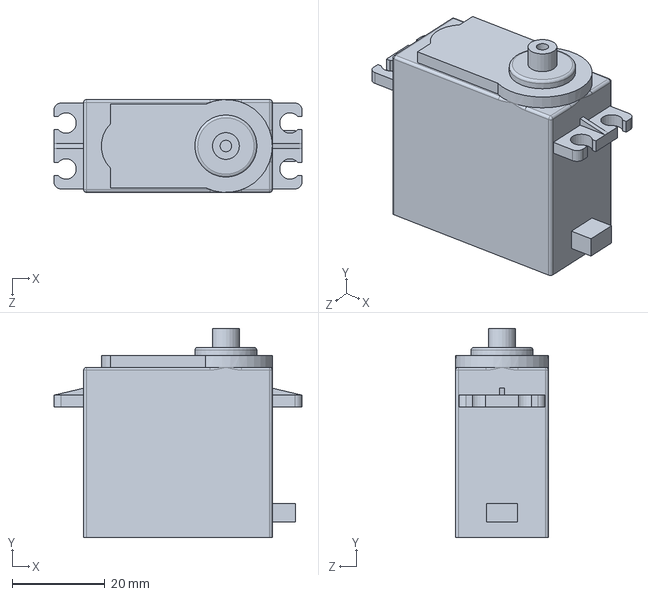
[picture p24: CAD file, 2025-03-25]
3d_model/external_parts/MG996R_servomotor.SLDPRT
53.4 x 45.1 x 20.0 mm

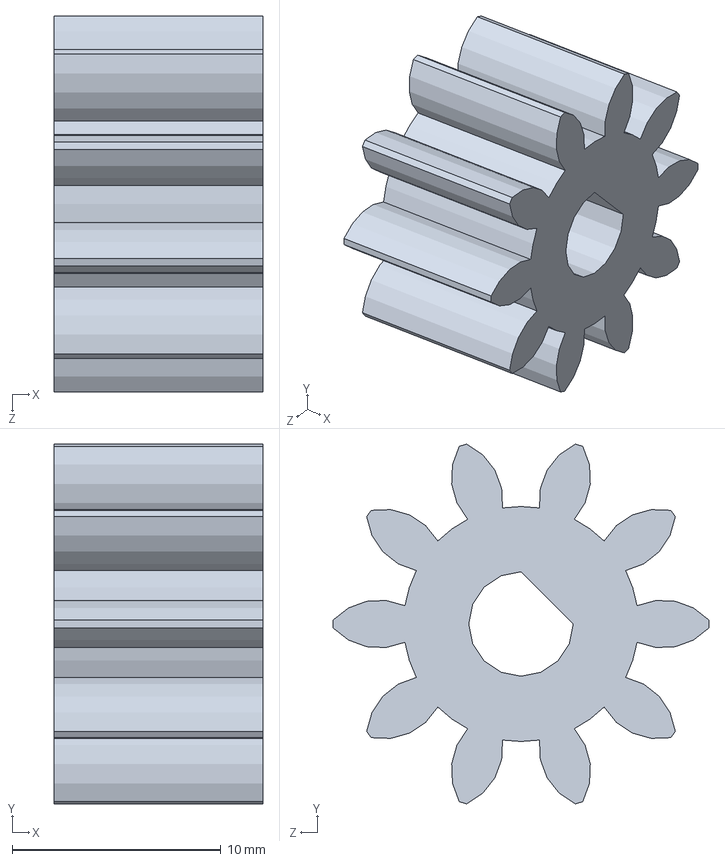
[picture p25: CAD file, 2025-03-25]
3d_model/gear_parts_n/stepper_gear_2.SLDPRT
10.0 x 17.2 x 18.0 mm

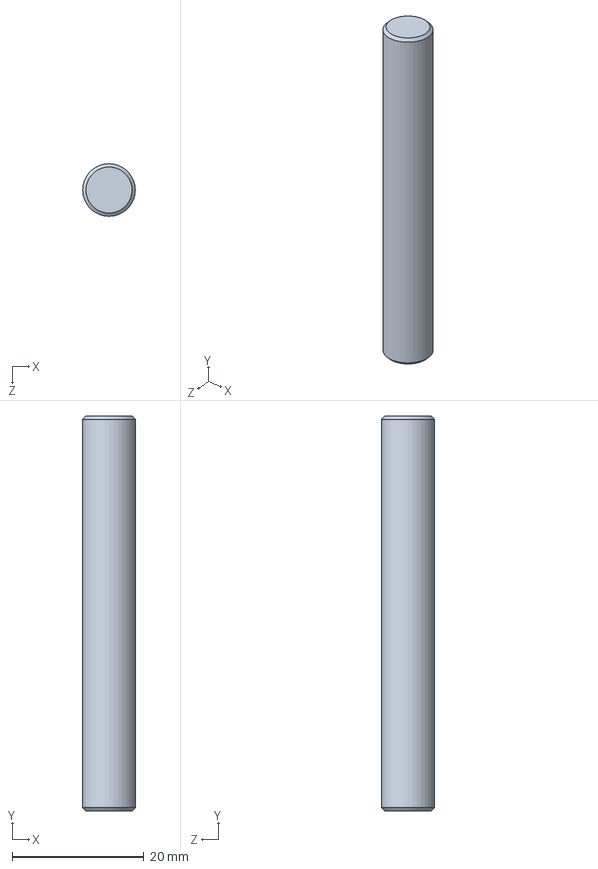
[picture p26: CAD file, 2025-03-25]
3d_model/j3_bar_parts.SLDPRT
8.00 x 60.0 x 8.00 mm

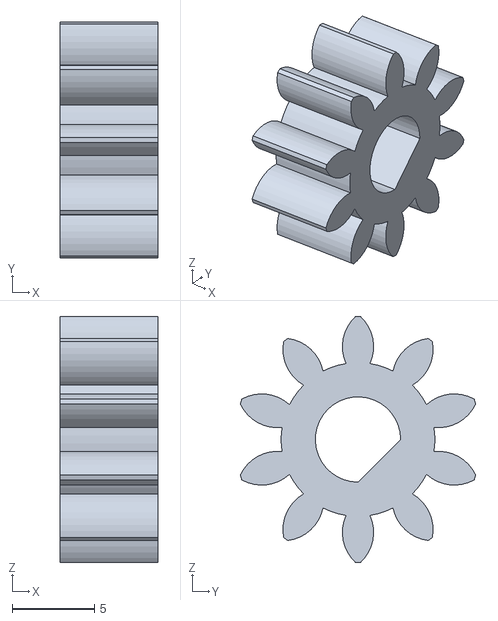
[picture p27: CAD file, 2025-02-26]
3d_model_2/printable_parts/stepper gear 1.25M.STL
6.00 x 14.4 x 15.0

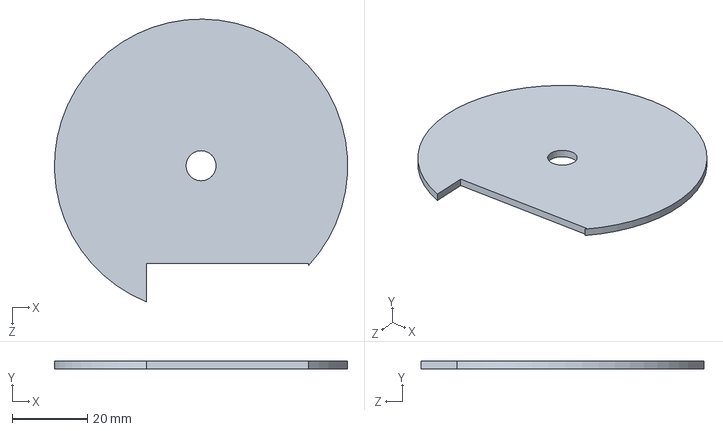
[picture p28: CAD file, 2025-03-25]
3d_model/additional parts/cover_sx_j2_1.SLDPRT
77.9 x 2.00 x 75.2 mm

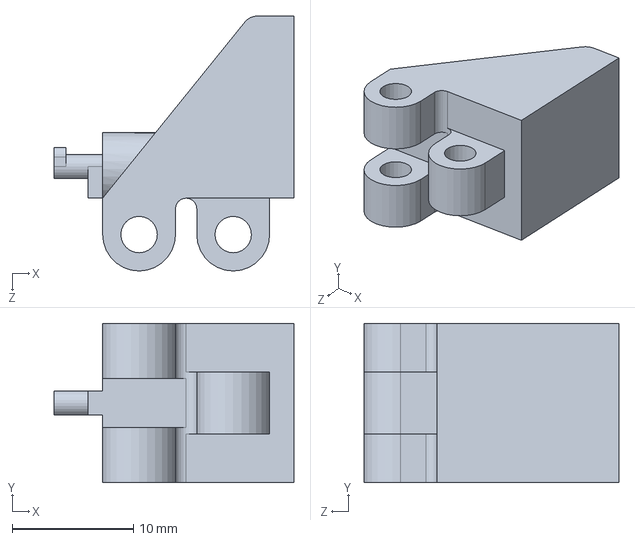
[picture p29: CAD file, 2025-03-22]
3d_model/endeffector_parts/Endeffector_adaptive_config-3f_1gdl/final_gripper_2.SLDPRT
19.8 x 13.1 x 21.0 mm

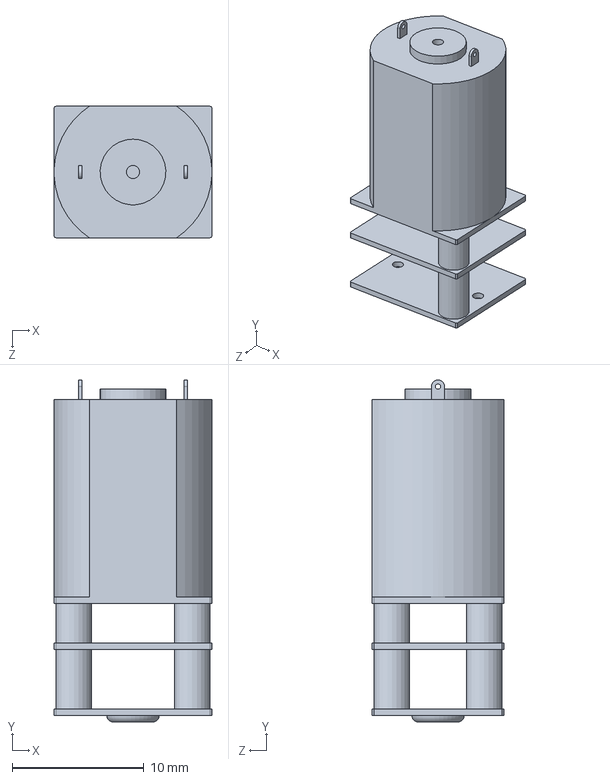
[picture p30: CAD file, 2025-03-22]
3d_model/endeffector_parts/Endeffector_static_config-3f/DC_motor_part.SLDPRT
12.0 x 26.0 x 10.0 mm

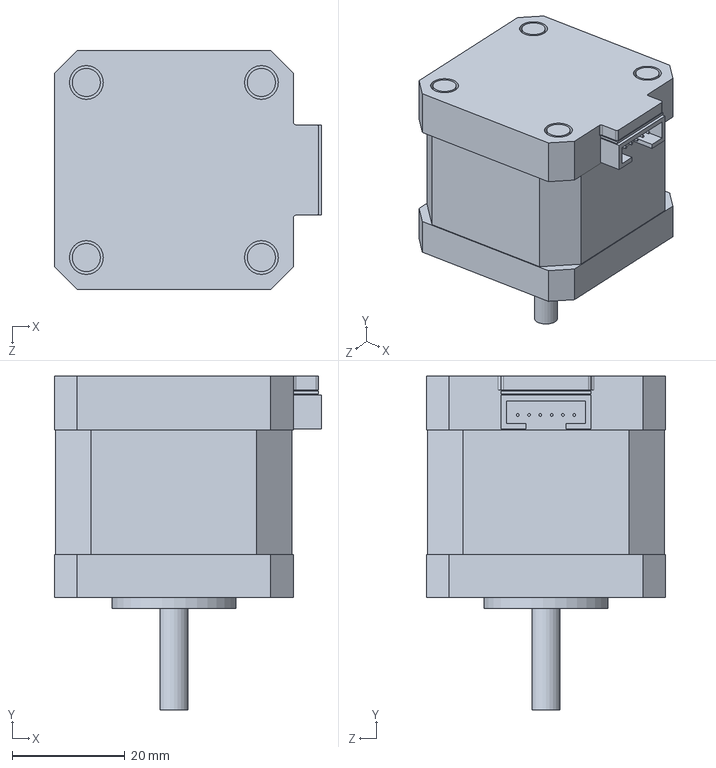
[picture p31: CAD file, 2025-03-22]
3d_model/External_parts/NEMA_17.SLDPRT
47.3 x 59.2 x 42.3 mm

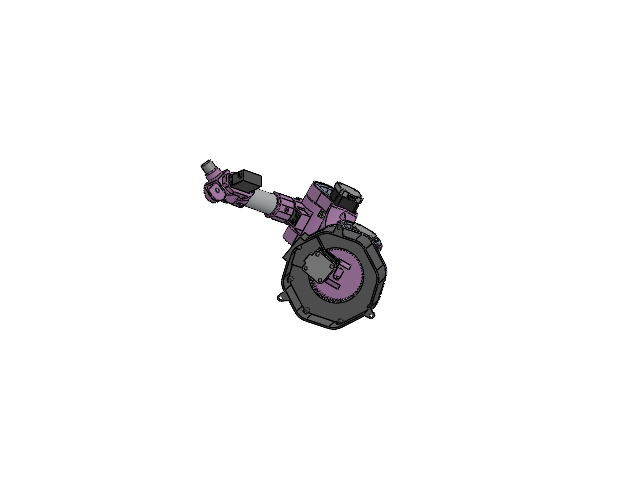
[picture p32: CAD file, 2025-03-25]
3d_model/Assem1.SLDASM
wrist_part_1
wrist_part_2
J3
support_j2
J2
j2_support
base_part_RSN
base_part_cover
gear_base
elektromagnet_endeffector
instrument ball bearing_68_am x 4
gear_j2 x 2
gear_j3
stepper_gear_1
stepper_gear_2 x 3
NEMA_17 x 4
MG996R_servomotor x 2
pinion_engagement_servomotor_2 x 2
electromagnet
cover_dx_j2_1
cover_dx_j2_2
cover_dx_j3_1
cover_dx_j3_2
cover_sx_j2_1
cover_sx_j2_2
cover_sx_j3_1
cover_sx_j3_2
top_tube
bottom_tube
j2_bar_parts
j3_bar_parts
j5_bar_parts

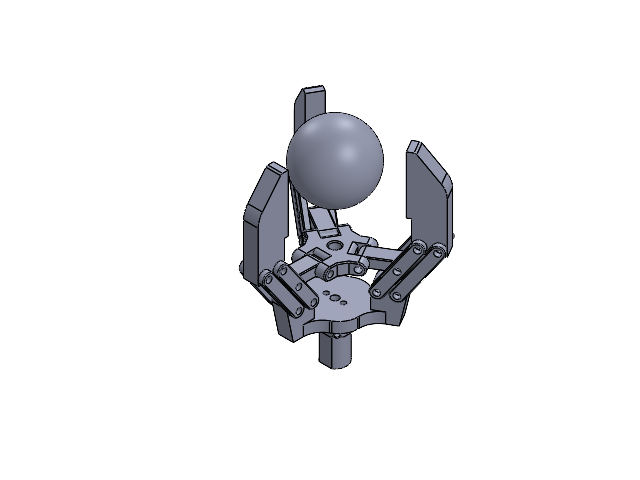
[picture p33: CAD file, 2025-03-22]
3d_model/endeffector_parts/Endeffector_static_config-3f/total.SLDASM
Base_part
Elevetor_part
Connecting_rod_3_part x 6
Connecting_rod_2_part x 6
Gripper1_part x 3
Connecting_rod_1_part x 3
DC_motor_part
ball

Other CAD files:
3d_model/endeffector_parts/Endeffector_adaptive_config-3f_1gdl/dito_assemblato.SLDASM
3d_model/endeffector_parts/Endeffector_adaptive_config-3f_1gdl/finger_assembly.SLDASM
3d_model/printable_parts/base_support_endeffector.STL
3d_model/endeffector_parts/base_support_endeffector.SLDPRT
3d_model/J2.SLDPRT
3d_model/J3.SLDPRT
3d_model/additional parts/cover_dx_j2_2.SLDPRT
3d_model/additional parts/cover_dx_j3_1.SLDPRT
3d_model/additional parts/cover_dx_j3_2.SLDPRT
3d_model/additional parts/cover_sx_j3_1.SLDPRT
3d_model/additional parts/cover_sx_j3_2.SLDPRT
3d_model/base_part_RSN.SLDPRT
3d_model/base_part_cover.SLDPRT
3d_model/bottom_tube.SLDPRT
3d_model/electromagnet.SLDPRT
3d_model/endeffector_parts/Endeffector_adaptive_config-3f_1gdl/Connecting_rod_2_part.SLDPRT
3d_model/endeffector_parts/Endeffector_adaptive_config-3f_1gdl/Connecting_rod_3_part.SLDPRT
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

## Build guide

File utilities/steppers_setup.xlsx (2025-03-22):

Joint | ARR min | PSC min | f min | ARR max | PSC max | f max | Rapp | microstepping | master timer (pwm) | slave timer
1 | 65535 | 4 | 256.35 | 19999 | 4 | 840.00 | 4.27 | 4 | TIM1 | TIM4
2 | 65535 | 4 | 256.35 | 32999 | 4 | 509.09 | 6 | 4 | TIM2 | TIM3
3 | 65535 | 4 | 256.35 | 1999 | 4 | 8400.00 | 4.9 | 8 | TIM8 | TIM5

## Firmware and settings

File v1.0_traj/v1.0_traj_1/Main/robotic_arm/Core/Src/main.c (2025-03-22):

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
/* Includes ------------------------------------------------------------------*/
#include "main.h"
#include "tim.h"
#include "gpio.h"

/* USER CODE BEGIN Includes */
#include "stepper.h"
#include "servo.h"

#define TRAPEZOIDAL_PROFILE /*COMMENT THIS IF YOU DON'T WANT THIS MOTION PROFILE FOR THE STEPPERS
 	 	 	 	 	 	 	 	AND ENABLE THE INTERRUPTS FOR THE SLAVE TIMERS*/

#ifdef TRAPEZOIDAL_PROFILE
#include "trapezoidal_profile.h"
#include "trapezoidal_profile.c"
#endif

#ifndef TRAPEZOIDAL_PROFILE
#include "stp_callback.c"
#endif

/* USER CODE END Includes */


/* USER CODE BEGIN PV */
static stepper_obj stp1;
static stepper_obj stp2;
static stepper_obj stp3;
static stepper_obj stp4;
static servo_obj srv1;
static servo_obj srv2;

/* USER CODE END PV */

void SystemClock_Config(void);
/**
  * @brief  The application entry point.
  * @retval int
  */
int main(void)
{

  /* MCU Configuration--------------------------------------------------------*/

  /* Reset of all peripherals, Initializes the Flash interface and the Systick. */
  HAL_Init();

  /* Configure the system clock */
  SystemClock_Config();

  /* Initialize all configured peripherals */
  MX_GPIO_Init();
  MX_TIM3_Init();
  MX_TIM5_Init();
  MX_TIM1_Init();
  MX_TIM2_Init();
  MX_TIM4_Init();
  MX_TIM8_Init();
  MX_TIM10_Init();
  MX_TIM11_Init();
  /* USER CODE BEGIN 2 */

	/*IF YOU'RE NOT USING THE TRAPEZOIDAL PROFILE USE THE HAL_TIM_BASE_START_IT*/
	HAL_TIM_Base_Start(&htim4); //start timer 1st joint
	HAL_TIM_Base_Start(&htim3); //start timer 2nd joint
	HAL_TIM_Base_Start(&htim5); //start timer 3rd joint

	HAL_GPIO_WritePin(ENABLE_GPIO_Port, ENABLE_Pin, GPIO_PIN_RESET); //ENABLE stepper motors

	/* stepper_init(obj, timer pwm, timer slave, resol, microstep, enable_port, direction_port */
	stepper_init(&stp1, &htim1, &htim4, 1.8, 4 * 4.27, DIRECTION1_GPIO_Port,
	DIRECTION1_Pin);
	stepper_init(&stp2, &htim2, &htim3, 1.8, 4 * 6, DIRECTION2_GPIO_Port,
	DIRECTION2_Pin);
	stepper_init(&stp3, &htim2, &htim3, 1.8, 4 * 6, DIRECTION3_GPIO_Port,
	DIRECTION3_Pin);
	stepper_init(&stp4, &htim8, &htim5, 1.8, 8 * 4.9, DIRECTION4_GPIO_Port,
	DIRECTION4_Pin);

	//servo: default position 0° in the range {-90,+90}
	/*servo_init(obj, timer pwm)*/
	servo_init(&srv1, &htim10);
	servo_init(&srv2, &htim11);



	for (int i = 0; i < 2; i++) { //trajectory repeated 2 times

		//1ST MOVEMENT
		stepper_move(&stp1, COUNTERCLOCKWISE, 36.5, 40);

		stepper_move(&stp2, CLOCKWISE, 132.5, 10);
		stepper_move(&stp3, COUNTERCLOCKWISE, 132.5, 10);

		stepper_move(&stp4, CLOCKWISE, 40, 40);

		servo_move(&srv2, -15);
		HAL_GPIO_TogglePin(ENDEFF_en_GPIO_Port, ENDEFF_en_Pin);

		HAL_Delay(3500);

		//2ND MOVEMENT

		stepper_move(&stp2, COUNTERCLOCKWISE, 75, 10);
		stepper_move(&stp3, CLOCKWISE, 75, 10);

		HAL_Delay(2000);

		//3RD MOVEMENT
		stepper_move(&stp1, CLOCKWISE, 70, 70);
		HAL_Delay(3900);

		//4TH MOVEMENT

		stepper_move(&stp2, CLOCKWISE, 45, 10);
		stepper_move(&stp3, COUNTERCLOCKWISE, 45, 10);


		servo_move(&srv2, 0);

		HAL_Delay(4000);

		//BACK TO INITIAL POSITION

		HAL_GPIO_TogglePin(ENDEFF_en_GPIO_Port, ENDEFF_en_Pin);

		stepper_move(&stp2, COUNTERCLOCKWISE, 104.5, 10);
		stepper_move(&stp3, CLOCKWISE, 104.5, 10);

		stepper_move(&stp1, COUNTERCLOCKWISE, 33.5, 40);

		stepper_move(&stp4, COUNTERCLOCKWISE, 40, 40);

		HAL_Delay(3000);
	}

  /* USER CODE END 2 */

  /* Infinite loop */
  /* USER CODE BEGIN WHILE */

	while (1) {

    /* USER CODE END WHILE */

    /* USER CODE BEGIN 3 */
	}
  /* USER CODE END 3 */
}

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


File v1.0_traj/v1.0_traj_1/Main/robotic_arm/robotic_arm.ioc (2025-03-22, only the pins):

Mcu.UserName=STM32F446RETx
PA0-WKUP.GPIO_Label=PWM2
PA0-WKUP.Signal=S_TIM2_CH1_ETR
PA1.GPIO_Label=PWM3
PA1.Signal=S_TIM2_CH2
PA13.GPIO_Label=TMS
PA13.Signal=SYS_JTMS-SWDIO
PA14.GPIO_Label=TCK
PA14.Signal=SYS_JTCK-SWCLK
PA2.GPIO_Label=USART_TX
PA2.Signal=USART2_TX
PA5.GPIO_Label=LD2 [Green Led]
PA5.Signal=GPIO_Output
PA6.GPIO_Label=DIRECTION4
PA6.Signal=GPIO_Output
PA7.GPIO_Label=DIRECTION3
PA7.Signal=GPIO_Output
PA8.GPIO_Label=PWM1
PA8.Signal=S_TIM1_CH1
PB0.GPIO_Label=DIRECTION1
PB0.Signal=GPIO_Output
PB1.GPIO_Label=SERVO_en
PB1.Signal=GPIO_Output
PB2.GPIO_Label=ENDEFF_en
PB2.Signal=GPIO_Output
PB3.GPIO_Label=SWO
PB3.Signal=SYS_JTDO-SWO
PB8.GPIO_Label=SERVO_1
PB8.Signal=S_TIM10_CH1
PB9.GPIO_Label=SERVO_2
PB9.Signal=S_TIM11_CH1
PC13.GPIO_Label=DISABLE_button
PC13.Signal=GPXTI13
PC14-OSC32_IN.Signal=RCC_OSC32_IN
PC15-OSC32_OUT.Signal=RCC_OSC32_OUT
PC4.GPIO_Label=DIRECTION2
PC4.Signal=GPIO_Output
PC5.GPIO_Label=ENABLE
PC5.Signal=GPIO_Output
PC6.GPIO_Label=PWM4
PC6.Signal=S_TIM8_CH1
PH0-OSC_IN.Signal=RCC_OSC_IN
PH1-OSC_OUT.Signal=RCC_OSC_OUT

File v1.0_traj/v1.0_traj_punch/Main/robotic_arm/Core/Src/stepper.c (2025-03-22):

#include <stepper.h>

//definisco la struct stepper con i seguenti parametri
void stepper_init(stepper_obj *stp, TIM_HandleTypeDef *pwm_timer,
		TIM_HandleTypeDef *position_timer, float stepper_resolution,
		uint16_t microstep, GPIO_TypeDef *direction_port,
		uint16_t direction_pin) {

	stp->position_timer = position_timer;
	stp->pwm_timer = pwm_timer;

	stp->direction_port = direction_port;
	stp->direction_pin = direction_pin;

	stp->stepper_resolution = stepper_resolution;
	stp->microstep = microstep;
	stp->step_per_rev = 360.0f / stepper_resolution; // 360°/resolution
	stp->step_scale = stp->step_per_rev * microstep;

}

int n_steps_a[3]; //3 pwm timers
int arr_des_a[3];

static int flag_configured_timer2; //for the timer2 config

float freq_des_steps; //DEBUG
static int arr_des = 20000;  //random value

void stepper_move(stepper_obj *stp, direction_str direction, float position,
		float freq_desired) {

	int i = 0;
	int n_steps = stp->step_scale * position / 360.0f; //[n_steps]

	freq_des_steps = stp->step_scale * freq_desired / 360.0f; //[n_steps/s]

	arr_des = (HAL_RCC_GetPCLK2Freq() * 2 / freq_des_steps)
			/ (stp->pwm_timer->Instance->PSC + 1) - 1;

	HAL_GPIO_WritePin(stp->direction_port, stp->direction_pin, direction); //DIRECTION

	if (stp->pwm_timer->Instance != TIM2) {

		//reset_timers(stp);

		__HAL_TIM_SET_AUTORELOAD(stp->position_timer,
				(n_steps * (stp->pwm_timer->Instance->PSC + 1)) - 1);
		__HAL_TIM_SET_COMPARE(stp->pwm_timer, TIM_CHANNEL_1,
				__HAL_TIM_GET_AUTORELOAD(stp->pwm_timer)/2);

		HAL_TIM_PWM_Start_IT(stp->pwm_timer, TIM_CHANNEL_1); //START PWM

	} else { //set parameters for the timer2 separately cause it has 2 channel
		if (flag_configured_timer2 != 1) { //this cause the second stepper must be equal to the first one

			//reset_timers(stp);
			__HAL_TIM_SET_AUTORELOAD(stp->position_timer,
					(n_steps * (stp->pwm_timer->Instance->PSC + 1)) - 1);
			__HAL_TIM_SET_COMPARE(stp->pwm_timer, TIM_CHANNEL_1,
					__HAL_TIM_GET_AUTORELOAD(stp->pwm_timer)/2);

			__HAL_TIM_SET_COMPARE(stp->pwm_timer, TIM_CHANNEL_2,
					__HAL_TIM_GET_AUTORELOAD(stp->pwm_timer)/2);

		} else {
			HAL_TIM_PWM_Start_IT(stp->pwm_timer, TIM_CHANNEL_1); //START PWM
			HAL_TIM_PWM_Start_IT(stp->pwm_timer, TIM_CHANNEL_2); //START PWM)

		}
		flag_configured_timer2 ^= 1;

	}
	n_steps = n_steps * (stp->pwm_timer->Instance->PSC + 1);

	if (stp->pwm_timer->Instance == TIM1) {
		i = 0;
	} else {
		if (stp->pwm_timer->Instance == TIM2) {
			i = 1;
		} else
			i = 2;
	}
	n_steps_a[i] = n_steps;
	arr_des_a[i] = arr_des;

}

void reset_timers(stepper_obj *stp) {

	stp->pwm_timer->Instance->EGR = TIM_EGR_UG; //reset the trigger
	//stp->position_timer->Instance->EGR = TIM_EGR_UG; //reset the trigger

}

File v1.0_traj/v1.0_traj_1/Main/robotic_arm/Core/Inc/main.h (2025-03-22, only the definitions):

#define DISABLE_button_Pin GPIO_PIN_13
#define DISABLE_button_GPIO_Port GPIOC
#define DISABLE_button_EXTI_IRQn EXTI15_10_IRQn
#define PWM2_Pin GPIO_PIN_0
#define PWM2_GPIO_Port GPIOA
#define PWM3_Pin GPIO_PIN_1
#define PWM3_GPIO_Port GPIOA
#define USART_TX_Pin GPIO_PIN_2
#define USART_TX_GPIO_Port GPIOA
#define LD2_Pin GPIO_PIN_5
#define LD2_GPIO_Port GPIOA
#define DIRECTION4_Pin GPIO_PIN_6
#define DIRECTION4_GPIO_Port GPIOA
#define DIRECTION3_Pin GPIO_PIN_7
#define DIRECTION3_GPIO_Port GPIOA
#define DIRECTION2_Pin GPIO_PIN_4
#define DIRECTION2_GPIO_Port GPIOC
#define ENABLE_Pin GPIO_PIN_5
#define ENABLE_GPIO_Port GPIOC
#define DIRECTION1_Pin GPIO_PIN_0
#define DIRECTION1_GPIO_Port GPIOB
#define SERVO_en_Pin GPIO_PIN_1
#define SERVO_en_GPIO_Port GPIOB
#define ENDEFF_en_Pin GPIO_PIN_2
#define ENDEFF_en_GPIO_Port GPIOB
#define PWM4_Pin GPIO_PIN_6
#define PWM4_GPIO_Port GPIOC
#define PWM1_Pin GPIO_PIN_8
#define PWM1_GPIO_Port GPIOA
#define TMS_Pin GPIO_PIN_13
#define TMS_GPIO_Port GPIOA
#define TCK_Pin GPIO_PIN_14
#define TCK_GPIO_Port GPIOA
#define SWO_Pin GPIO_PIN_3
#define SWO_GPIO_Port GPIOB
#define SERVO_1_Pin GPIO_PIN_8
#define SERVO_1_GPIO_Port GPIOB
#define SERVO_2_Pin GPIO_PIN_9
#define SERVO_2_GPIO_Port GPIOB

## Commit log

2025-02-26 upload starter files repository
    [Assem1.SLDASM, Base_part.SLDPRT, J3.SLDPRT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]
2025-02-26 update J3 part dimensions
    [Assem1.SLDASM, J3.SLDPRT]
2025-02-26 manual+updated stepper test
2025-02-26 Joint 3 3d model update
    [Assem1.SLDASM, Base_part.SLDPRT, J2.SLDPRT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]
2025-03-01 updated stepper test
    -added a second timer to count the steps and so the position
    -position control pdf
2025-03-01 updated stepper
    library angular position control
2025-03-02 added servo script
    servo pwm 50hz script
2025-03-02 servo lib v0.1
    added servo lib
2025-03-02 added emergency button
    -added emergency button
    -servo datash
2025-03-03 update 3d model
    [Assem1.SLDASM, J3.SLDPRT, J3.STL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]
2025-03-06 updated
    --priority group fixed
    --reset timers function
    [robotic_arm.ioc, stepper.c, tim.c]
2025-03-06 hot updated
    added 4 steppers control
2025-03-06 fixed
    --priority group
    --"microstepping" adjusted w prescaler
    [main.c, robotic_arm.ioc, tim.c]
2025-03-09 updated stepper lib
2025-03-10 3d model update
    [Assem1.SLDASM, Base_part.SLDPRT, J2.SLDPRT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]
2025-03-11 fixed servo lib
2025-03-12 v0.1.2
    tested fixed version
    [main.c, robotic_arm.ioc, stepper.c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]
2025-03-13 updated stepper.c
    --fixed the second iteration set parameters of the timer2
    --tidied
    [main.c, stepper.c]
2025-03-13 updated
    --updated stepper.c from testing
    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
2025-03-13 to be tested
    [steppers_setup.xlsx]
2025-03-14 to improve
    --constant velocity to be fixed
    [main.c, tim.c]
2025-03-14 to be fixed
    fix the n_steps
    [main.c, tim.c]
2025-03-15 endeffector to support the electromagnet
    [Assem1.SLDASM, base_gear.SLDPRT, base_gear_1.SLDPRT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]
2025-03-15 fix
    --added start arr constraint
    [tim.c]
2025-03-16 updated
    --updated servo.c default pos
    --var type
    --stepper.c fix
    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
    [main.c, robotic_arm.ioc, servo.c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]
2025-03-17 fix tim1 configuration interrupt
    [main.c, robotic_arm.ioc, tim.c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]
2025-03-18 Add J2 part to 3d model
    [Assem1.SLDASM, Base_part.SLDPRT, Connecting_rod_1_part.SLDPRT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]
2025-03-18 UPT/FIX management timers
2025-03-18 add Kicad schematic and stm32 report
    [RASN5.kicad_pcb, RASN5.kicad_sch]
2025-03-20 test on adaptive end-effector
    [j2_support.SLDPRT]
2025-03-25 update schematic and pinout report
    [Assem1.SLDASM, Base_part.SLDPRT, J3.SLDPRT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]

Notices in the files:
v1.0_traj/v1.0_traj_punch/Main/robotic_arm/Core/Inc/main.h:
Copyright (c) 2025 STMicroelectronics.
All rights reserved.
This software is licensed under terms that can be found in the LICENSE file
